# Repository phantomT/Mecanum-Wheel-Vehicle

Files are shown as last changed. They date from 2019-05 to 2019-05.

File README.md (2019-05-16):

# 麦克纳姆轮机器人-Mecanum Wheel Robot

## 电路说明-Circuit Description

### 电路连线-Circuit Connection：

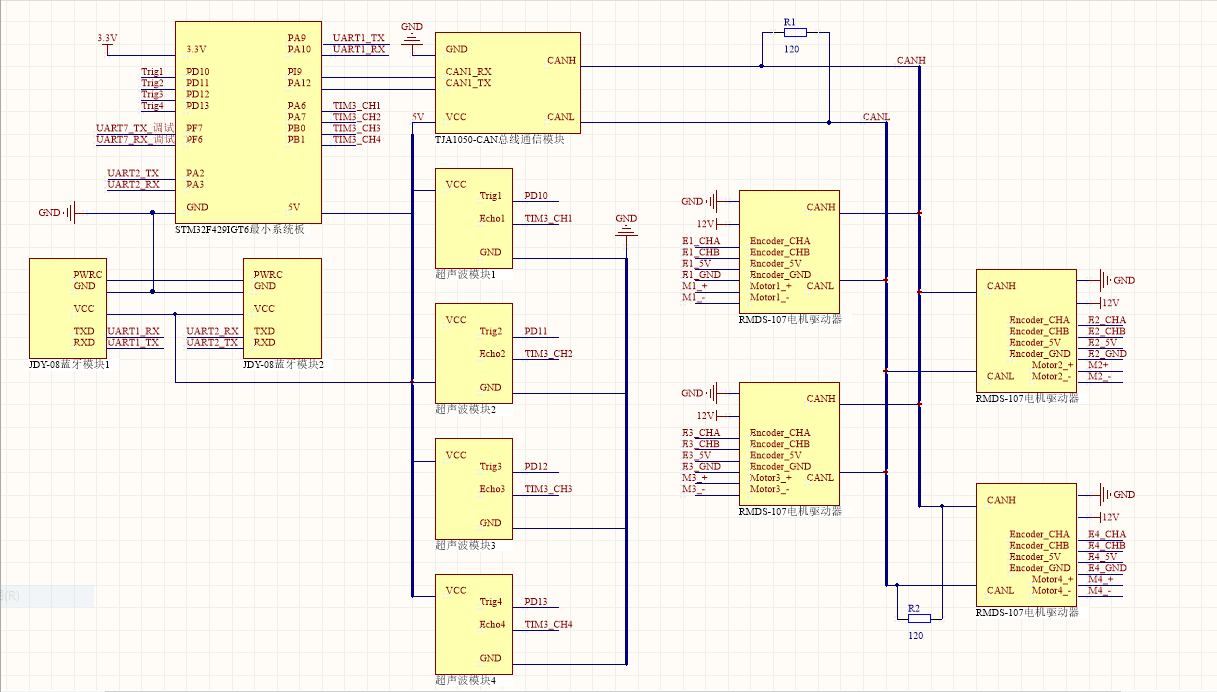
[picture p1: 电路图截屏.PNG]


### 电路元件-Circuit Components：

1. STM32F429IGT6最小系统板——控制板

   > STM32F429IGT6 Minimum System Board - Control Board (MCU)

2. TJA1050 CAN总线通信模块

   > TJA1050 CAN bus communication Module

3. JDY-08蓝牙模块

   > JDY-08 Bluetooth Module

4. 超声波传感器

   > Ultrasonic Sensor

5. RMDS-107直流电机驱动器

   > RMDS-107 DC Motor Driver

控制板使用 UART 1 和 2 接口与蓝牙模块通信，发送指令接受信号强度回传。  

The MCU communicates with the Bluetooth Module using the UART 1 and 2 interfaces, and sends commands to receive signal strength backhaul.    

UART 7 接口用于测试调试，PI9 和 PA12 是 CAN 协议通信引脚，通过 TJA1050 模块转换接入 CAN 总线，对电机驱动器进行控制。    

The UART 7 interface is used for test debugging. PI9 and PA12 are CAN Bus Communication pins. The TJA1050 Module is connected to the CAN Bus to control the Motor Driver.    

CAN总线两端各接入一个120Ω的电阻，每个驱动器控制一个直流编码电机，Encoder 接口接入编码器的 AB 相信号线和 5V 电源线和地线，Motor 线接入电机的正负极。  

Each **120Ω Resistor** is connected to each end of the CAN Bus. Each Driver controls a DC-coded motor. The `Encoder` interface is connected to the AB-phase signal line of the Encoder and the `5V` and `GND`. The `motor` line is connected to the `+` and `-` of the Motor.   

使用 MCU 上 TIM 3 计时器的四个通道对应的引脚，接受超声波传感器的回传信号，使用控制板的 PD10-PD13 四个 GPIO 引脚向超声波模块传输触发信号。  

Use the corresponding pin of the 4 channels of TIM3 on the MCU to receive the return signal of the Ultrasonic Sensor, and use the four GPIO pins from PD10 to PD13 on the MCU to trigger 4 Ultrasonic Modules.   

**控制板由锂电池接入电源模块降压提供的 3.3V 电源供电，驱动器电源由锂电池直接接入，使用 12V 电源，驱动器直接为编码器和电机供电。**传感器使用的 5V 电源由控制板内置的变压模块提供。  

The MCU is powered by a 3.3V power supply which voltage was reduced by a  Power Module from a Lithium Battery. The Driver's power supply is directly connected to the Lithium Battery. The 12V power supply is used, and the Driver directly supplies power to the Encoder and the Motor. The 5V power supply used by Sensors is provided by the transformer built-in the MCU.    

**程序中只包含CAN总线通信与电机驱动部分代码。**  

The program only contains the CAN bus communication and motor driver  code.      

## 机械设计-Mechanical Design

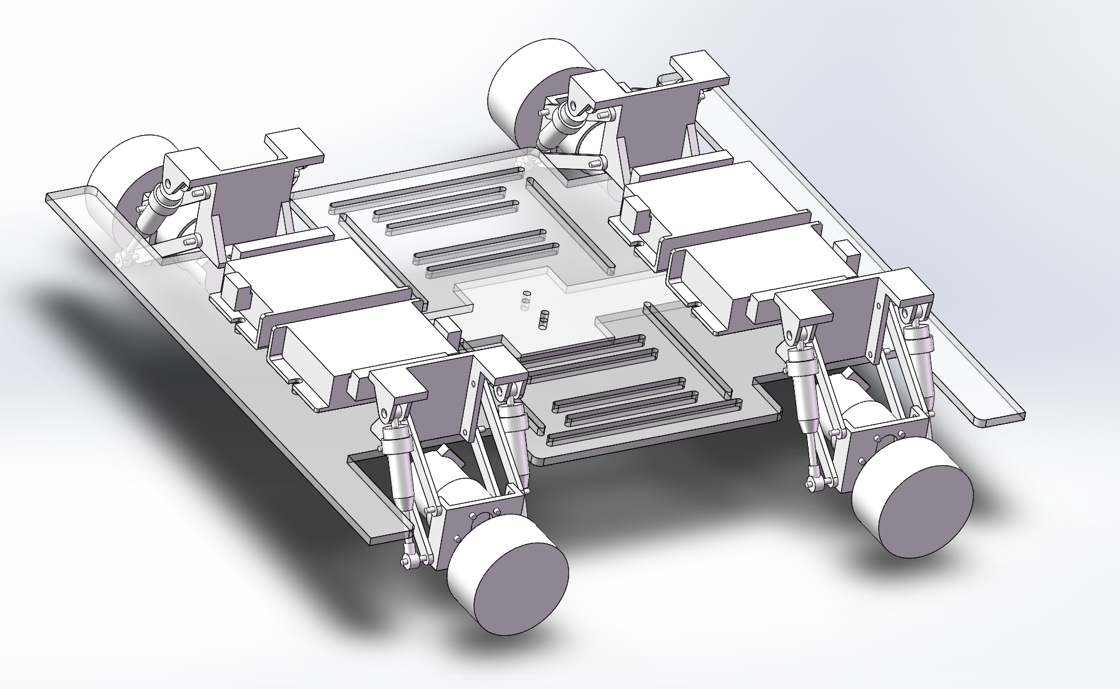
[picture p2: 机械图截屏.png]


机械图纸包含在`Mechanics`文件夹里  

Mechanical drawings are included in the `Mechanics` folder.

## 驱动程序

**程序中只包含CAN总线通信与电机驱动部分代码。**  

The program only contains the CAN bus communication and motor driver  code.    

CAN总线程序与电机驱动程序移植自`Robomodule`厂家提供的库函数模板。  

The CAN bus program and the motor driver are ported from the library function template provided by the manufacturer of `Robomodule`.  

程序使用**STM32CUBEMX**配置，使用**HAL**库进行编程。  

The program uses the **STM32CUBEMX** to configure the chip and is programmed using the **HAL** library.  

程序源码包含在`SourceCode`文件夹里。  

The program source code is included in the `SourceCode` folder.

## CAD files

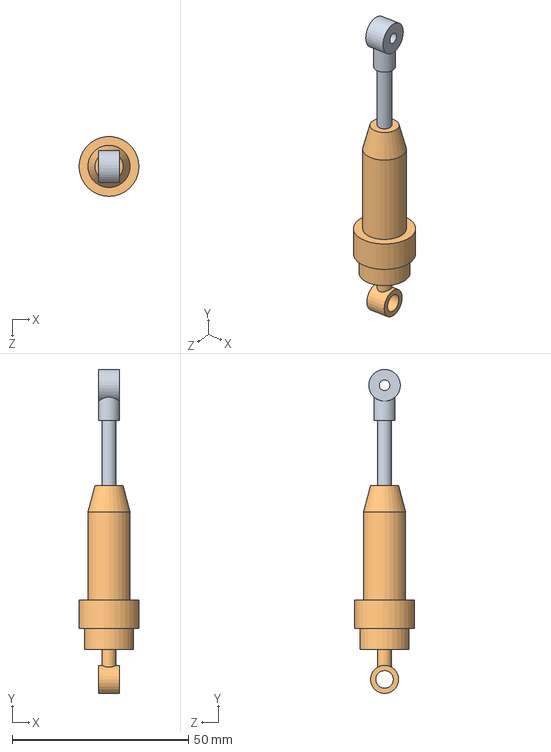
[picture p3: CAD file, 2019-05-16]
Mechanics/避震器简化.SLDASM
17.0 x 91.9 x 17.0 mm
避震器简化
避震器下简化

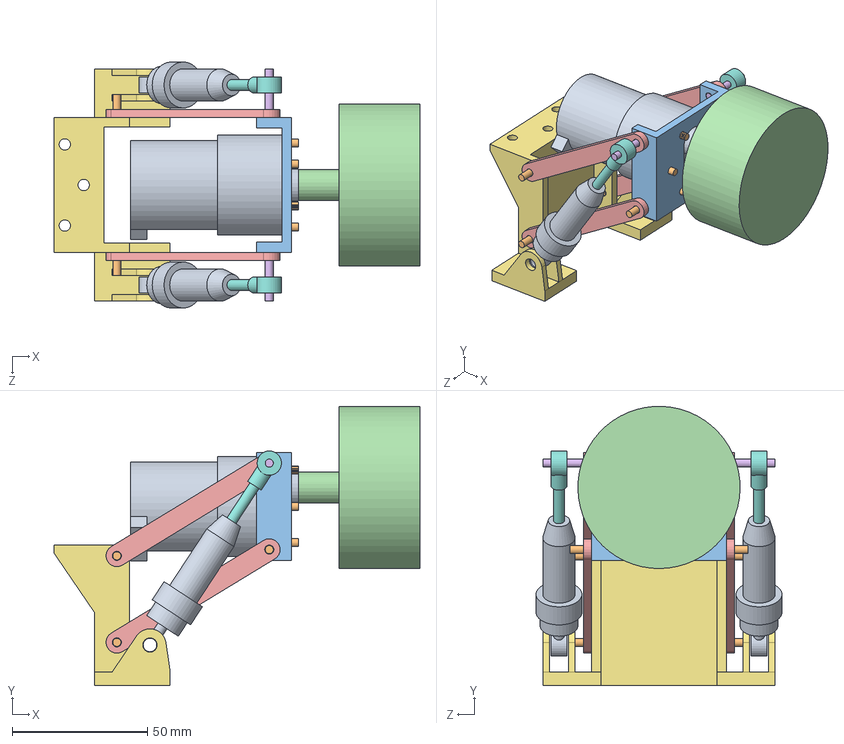
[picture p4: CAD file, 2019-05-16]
Mechanics/悬挂.SLDASM
135.4 x 103.3 x 91.0 mm
37mm电机简化
M3-12螺丝简化 x 13
双叉连接
麦轮简化
双叉连杆 x 4
M3-16螺丝简化 x 2
弹簧支架
避震器简化 x 2
避震器下简化 x 2

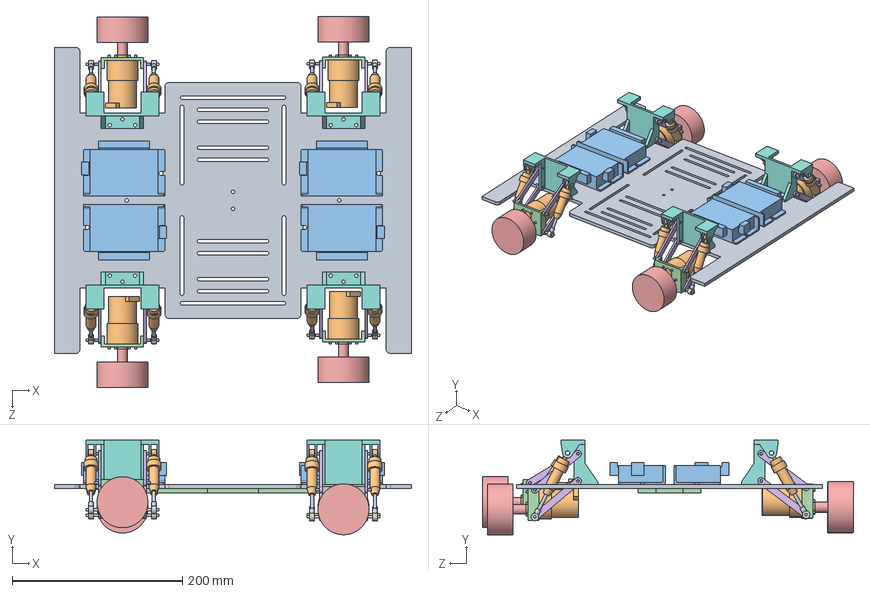
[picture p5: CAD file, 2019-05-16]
Mechanics/车体.SLDASM
420.0 x 111.2 x 436.5 mm
底板
37mm电机简化 x 4
M3-12螺丝简化 x 52
双叉连接 x 4
麦轮简化 x 4
双叉连杆 x 16
M3-16螺丝简化 x 8
弹簧支架 x 4
避震器简化 x 8
避震器下简化 x 8
CAN驱动器简化 x 4
加强板

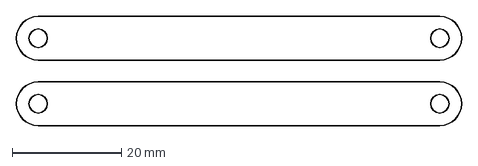
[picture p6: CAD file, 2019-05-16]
Mechanics/doublelink3.dxf
81.5 x 20.0 mm

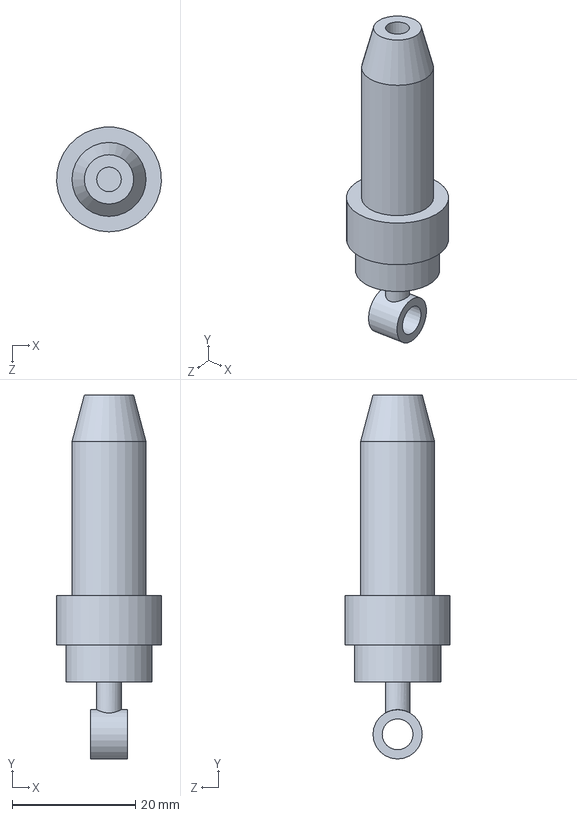
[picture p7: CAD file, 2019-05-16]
Mechanics/避震器下简化.SLDPRT
17.0 x 59.0 x 17.0 mm

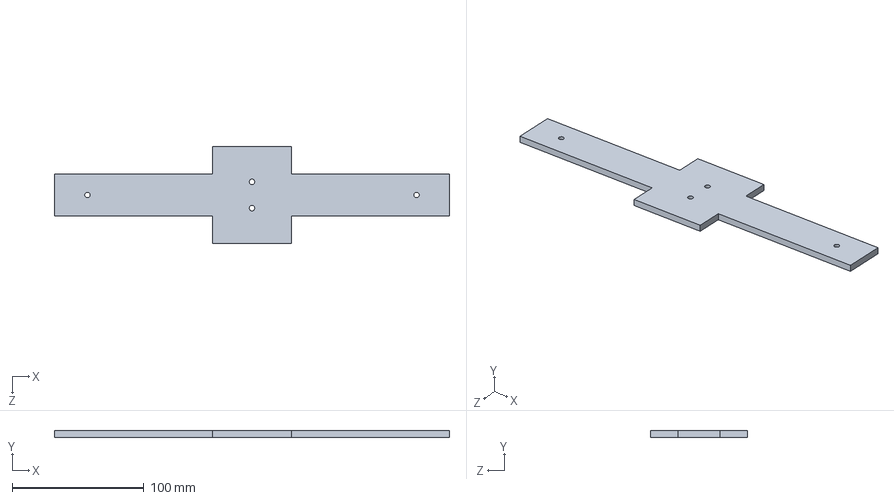
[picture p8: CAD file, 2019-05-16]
Mechanics/加强板.SLDPRT
300.0 x 5.00 x 74.0 mm

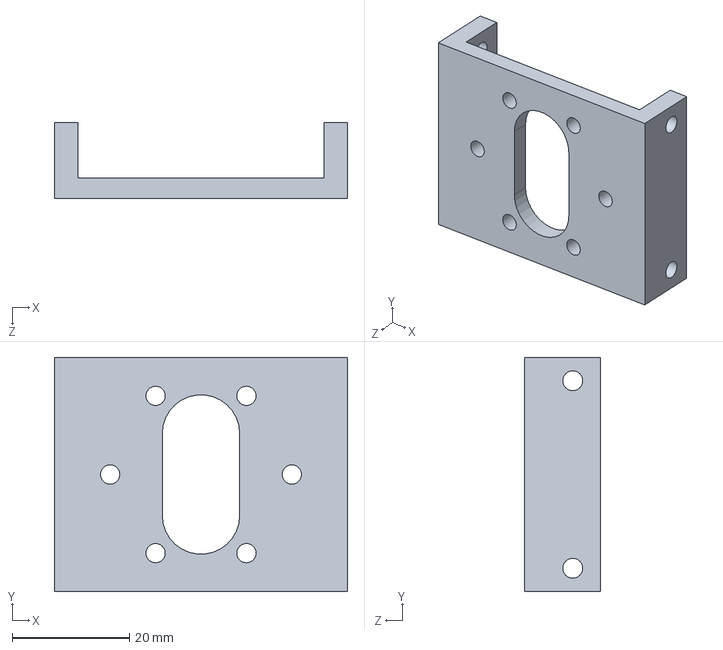
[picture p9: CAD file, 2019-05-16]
Mechanics/双叉连接.SLDPRT
50.0 x 40.0 x 13.0 mm

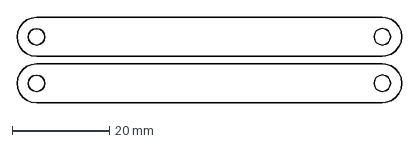
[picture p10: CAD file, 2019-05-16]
Mechanics/doublelink4.dxf
79.4 x 17.8 mm

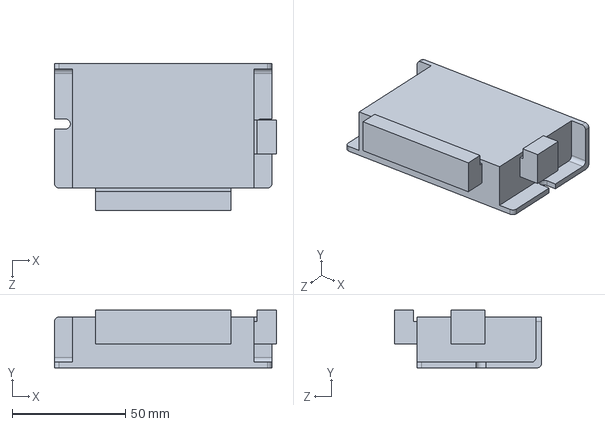
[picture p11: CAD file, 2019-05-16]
Mechanics/CAN驱动器简化.SLDPRT
98.0 x 25.5 x 65.0 mm

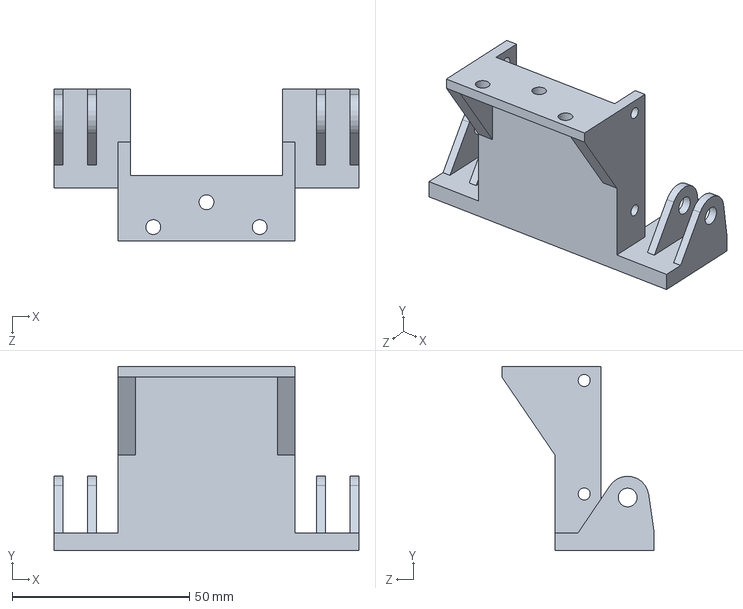
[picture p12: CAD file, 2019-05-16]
Mechanics/弹簧支架.SLDPRT
86.0 x 52.0 x 43.0 mm

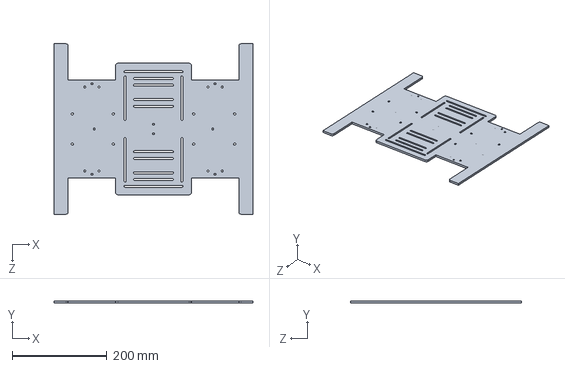
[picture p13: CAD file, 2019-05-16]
Mechanics/底板.SLDPRT
420.0 x 5.00 x 360.0 mm

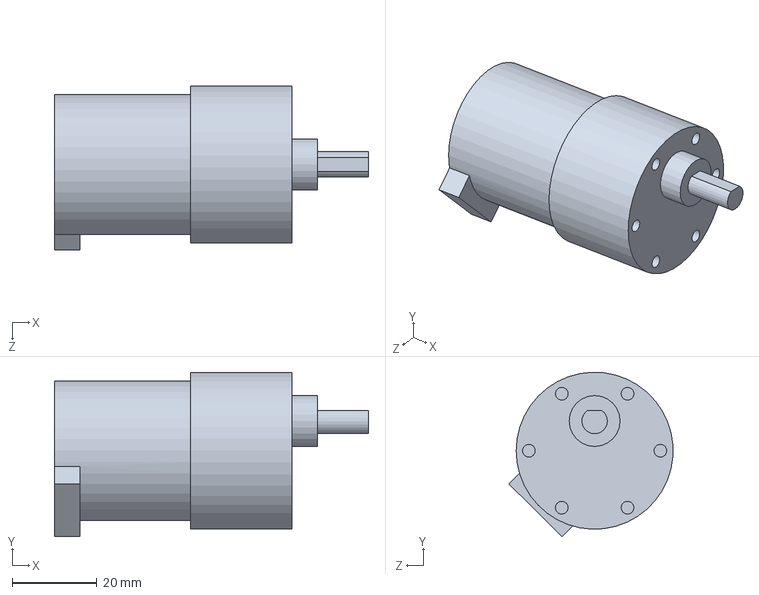
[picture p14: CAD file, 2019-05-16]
Mechanics/37mm电机简化.SLDPRT
74.0 x 38.8 x 38.7 mm

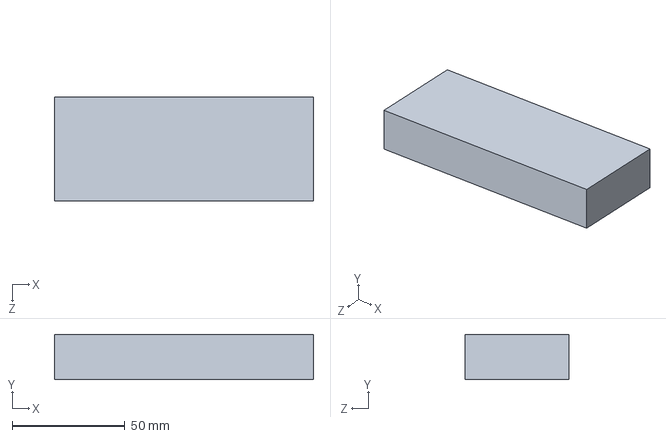
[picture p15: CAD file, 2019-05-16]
Mechanics/电池.SLDPRT
115.0 x 20.0 x 46.0 mm

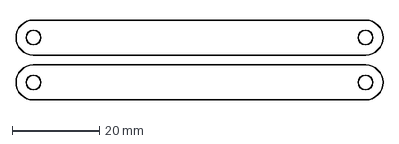
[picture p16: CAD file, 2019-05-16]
Mechanics/doublelink2.dxf
84.0 x 18.3 mm

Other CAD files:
Mechanics/双叉连杆.SLDPRT
Mechanics/麦轮简化.SLDPRT
Mechanics/doublelink.dxf
Mechanics/M3-12螺丝简化.SLDPRT
Mechanics/M3-16螺丝简化.SLDPRT
Mechanics/doublelink.dwg
Mechanics/doublelink2.dwg
Mechanics/doublelink3.dwg
Mechanics/底板.DXF
Mechanics/避震器简化.SLDPRT

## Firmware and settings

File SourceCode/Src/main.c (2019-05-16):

/**
  ******************************************************************************
  * File Name          : main.c
  * Description        : Main program body
  ******************************************************************************
  ** This notice applies to any and all portions of this file
  * that are not between comment pairs USER CODE BEGIN and
  * USER CODE END. Other portions of this file, whether 
  * inserted by the user or by software development tools
  * are owned by their respective copyright owners.
  *
  * COPYRIGHT(c) 2018 STMicroelectronics
  *
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
  ******************************************************************************
  */

/* Includes ------------------------------------------------------------------*/
#include "main.h"
#include "stm32f4xx_hal.h"
#include "can.h"
#include "usart.h"
#include "gpio.h"


/* USER CODE BEGIN PV */

	PID pid = 
{
	10000,	//输出限幅
	1.5,	//目标控制量(distance[m])
	0,	//反馈控制量(distance[m])

	100,	//Kp
	0.5,	//Ki
	0.1,	//Kd
	
	0, 0, 0	//e
};

int Temp_PWM = 5000;
char direct;
float MIN_LIMIT = 0;
float MAX_LIMIT = 10000;

/* USER CODE END PV */

void SystemClock_Config(void);

/* USER CODE BEGIN PFP */

/* USER CODE END PFP */

int main(void)
{

  /* USER CODE BEGIN 1 */
	short temp_velocity = 0;
  /* USER CODE END 1 */

  /* MCU Configuration----------------------------------------------------------*/

  /* Reset of all peripherals, Initializes the Flash interface and the Systick. */
  HAL_Init();

  /* USER CODE BEGIN Init */
	HAL_Delay(10000);
  /* USER CODE END Init */

  /* Configure the system clock */
  SystemClock_Config();

  /* Initialize all configured peripherals */
  MX_GPIO_Init();
  MX_CAN1_Init();
  MX_USART1_UART_Init();
  MX_USART2_UART_Init();

  /* USER CODE BEGIN 2 */
	delay_ms(500);                                      //刚开始要有足够的延时，确保驱动器已经初始化完成 
  CAN_RoboModule_DRV_Reset(0,0);                      //对0组所有驱动器进行复位 
    
  delay_ms(500);                                      //发送复位指令后的延时必须要有，等待驱动器再次初始化完成
    
  CAN_RoboModule_DRV_Config(0,1,100,0);               //1号驱动器配置为100ms传回一次数据
  delay_us(200);                                      //此处延时为了不让传回数据时候4个不一起传
  CAN_RoboModule_DRV_Config(0,2,100,0);               //2号驱动器配置为100ms传回一次数据
  delay_us(200);                                      //此处延时为了不让传回数据时候4个不一起传
  CAN_RoboModule_DRV_Config(0,3,100,0);               //3号驱动器配置为100ms传回一次数据
  delay_us(200);                                      //此处延时为了不让传回数据时候4个不一起传
  CAN_RoboModule_DRV_Config(0,4,100,0);               //3号驱动器配置为100ms传回一次数据

    
  CAN_RoboModule_DRV_Mode_Choice(0,0,Velocity_Mode);  //0组的所有驱动器 都进入速度模式
  delay_ms(500);                                      //发送模式选择指令后，要等待驱动器进入模式就绪。所以延时也不可以去掉。
    
  temp_velocity = 0;
  /* USER CODE END 2 */

  /* Infinite loop */
  /* USER CODE BEGIN WHILE */
  while (1)
  {
  /* USER CODE END WHILE */

  /* USER CODE BEGIN 3 */
		break;
  }
	
	temp_velocity = 5000;
	
	while(1)
	{
			delay_ms(300);
			CAN_Go_front_back(5000,temp_velocity);
			temp_velocity -= 500;
			if(temp_velocity<0)
			{
				break;
			}
	}
	
	temp_velocity = 5000;
	while(1)
	{
			delay_ms(300);
			CAN_Go_front_back(5000,-temp_velocity);
			temp_velocity-=500;
			if(temp_velocity<0)
			{
				break;
			}
	}
	
	temp_velocity = 5000;	
	while(1)
	{
			delay_ms(300);
			CAN_Go_left_right(5000,temp_velocity);
			temp_velocity-=500;
			if(temp_velocity<0)
			{
				break;
			}
	}
	
	temp_velocity = 5000;	
	while(1)
	{
			delay_ms(300);
			CAN_Go_left_right(5000,-temp_velocity);
			temp_velocity-=500;
			if(temp_velocity<0)
			{
				break;
			}
	}
	
	temp_velocity = 5000;	
	while(1)
	{
			delay_ms(300);
			CAN_deflect_left_right(5000,temp_velocity);
			temp_velocity-=500;
			if(temp_velocity<0)
			{
				break;
			}
	}
	
	temp_velocity = 5000;	
	while(1)
	{
			delay_ms(300);
			CAN_deflect_left_right(5000,-temp_velocity);
			temp_velocity-=500;
			if(temp_velocity<0)
			{
				break;
			}
	}
    
  temp_velocity = 0; 
  CAN_RoboModule_DRV_Velocity_Mode(0,0,5000,temp_velocity);
	
	/*
	while(1)
	{
		dis_v(distance,'w',*pid,Temp_PWM);
	}
	*/
	
  /* USER CODE END 3 */

}

/** System Clock Configuration
*/
void SystemClock_Config(void)
{

  RCC_OscInitTypeDef RCC_OscInitStruct;
  RCC_ClkInitTypeDef RCC_ClkInitStruct;

    /**Configure the main internal regulator output voltage 
    */
  __HAL_RCC_PWR_CLK_ENABLE();

  __HAL_PWR_VOLTAGESCALING_CONFIG(PWR_REGULATOR_VOLTAGE_SCALE1);

    /**Initializes the CPU, AHB and APB busses clocks 
    */
  RCC_OscInitStruct.OscillatorType = RCC_OSCILLATORTYPE_HSE;
  RCC_OscInitStruct.HSEState = RCC_HSE_ON;
  RCC_OscInitStruct.PLL.PLLState = RCC_PLL_ON;
  RCC_OscInitStruct.PLL.PLLSource = RCC_PLLSOURCE_HSE;
  RCC_OscInitStruct.PLL.PLLM = 25;
  RCC_OscInitStruct.PLL.PLLN = 360;
  RCC_OscInitStruct.PLL.PLLP = RCC_PLLP_DIV2;
  RCC_OscInitStruct.PLL.PLLQ = 4;
  if (HAL_RCC_OscConfig(&RCC_OscInitStruct) != HAL_OK)
  {
    _Error_Handler(__FILE__, __LINE__);
  }

    /**Activate the Over-Drive mode 
    */
  if (HAL_PWREx_EnableOverDrive() != HAL_OK)
  {
    _Error_Handler(__FILE__, __LINE__);
  }

    /**Initializes the CPU, AHB and APB busses clocks 
    */
  RCC_ClkInitStruct.ClockType = RCC_CLOCKTYPE_HCLK|RCC_CLOCKTYPE_SYSCLK
                              |RCC_CLOCKTYPE_PCLK1|RCC_CLOCKTYPE_PCLK2;
  RCC_ClkInitStruct.SYSCLKSource = RCC_SYSCLKSOURCE_PLLCLK;
  RCC_ClkInitStruct.AHBCLKDivider = RCC_SYSCLK_DIV1;
  RCC_ClkInitStruct.APB1CLKDivider = RCC_HCLK_DIV4;
  RCC_ClkInitStruct.APB2CLKDivider = RCC_HCLK_DIV2;

  if (HAL_RCC_ClockConfig(&RCC_ClkInitStruct, FLASH_LATENCY_5) != HAL_OK)
  {
    _Error_Handler(__FILE__, __LINE__);
  }

    /**Configure the Systick interrupt time 
    */
  HAL_SYSTICK_Config(HAL_RCC_GetHCLKFreq()/1000);

    /**Configure the Systick 
    */
  HAL_SYSTICK_CLKSourceConfig(SYSTICK_CLKSOURCE_HCLK);

  /* SysTick_IRQn interrupt configuration */
  HAL_NVIC_SetPriority(SysTick_IRQn, 0, 0);
}

/* USER CODE BEGIN 4 */
void dis_v(float distance,char direct,PID *pid,int Temp_PWM)
{
		float inc_val;
		float control_val=0;
		pid->feedback = distance;
	
		inc_val = pid_calc(pid);  
		control_val += inc_val;  
		control_val = range(control_val, MIN_LIMIT, MAX_LIMIT); 
		CAN_movement(direct, Temp_PWM,(int)control_val);
}
/* USER CODE END 4 */
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


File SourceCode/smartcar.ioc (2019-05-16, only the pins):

Mcu.UserName=STM32F429IGTx
PA10.Signal=USART1_RX
PA12.GPIO_Label=CAN1_TX_1000kbps
PA12.Signal=CAN1_TX
PA13.Signal=SYS_JTMS-SWDIO
PA14.Signal=SYS_JTCK-SWCLK
PA2.Signal=USART2_TX
PA3.Signal=USART2_RX
PA9.Signal=USART1_TX
PB11.Signal=GPIO_Output
PC14/OSC32_IN.Signal=RCC_OSC32_IN
PC15/OSC32_OUT.Signal=RCC_OSC32_OUT
PH0/OSC_IN.Signal=RCC_OSC_IN
PH1/OSC_OUT.Signal=RCC_OSC_OUT
PI9.GPIO_Label=CAN1_RX_1000kbps
PI9.Signal=CAN1_RX

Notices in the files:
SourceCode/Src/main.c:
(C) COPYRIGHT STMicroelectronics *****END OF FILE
